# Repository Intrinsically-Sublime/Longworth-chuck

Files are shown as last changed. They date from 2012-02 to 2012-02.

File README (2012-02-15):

---Description---

Credit for the movement should go to the late Mr. Longworth of the Hunter Valley Woodturning Club, New South Wales, Australia.

Thanks to Hexitex for turning Mr. Longworth's desgin into a printable design.

All the files are oriented and scaled for printing already.

Changes

I Reduced its diameter to 85mm and changed it to a three jaw design. I then designed a system to lock it with out a wrench.

How the lock works

The front face is now supported by three short lengths of 5/16" (8mm) smooth rod that go through large holes in the guide and sit against the base. When you turn the lock ring it turns the planets/nuts that pull the guide back and it pulls the screws holding the jaws back against the now supported face.

( you could eliminate the smooth rods by making the outside of the face extend back far enough to rest on the lip of the base. )

Updates
jun 10/11 . Added jaw_guide.stl It keeps the jaws aligned while tightening.

jun 9/11 . Replaced jaws with angled jaws inspired by MarkU's design thingiverse.com/thing:9186 except mine are sloped on both sides so only one set is needed.

Video
youtube.com/watch?v=V_vG_LOLz4s
Instructions

--Four jaw version--

Simplified keyless chuck NOW WITH FOUR JAWS !!!!!!!!

This is untested but based on a working design.

I started over this time to guarantee symmetry.

Removed the need for smooth metal rod.

Increased thickness of face plate.

Added fourth jaw.

Increased ring gear strength.

Removed the need for machine screws with screw head or socket head. You can now use hex head bolts.

Only uses 8 machine screws / bolts with nuts.

Eight washers optional. (under planet gears and under the heads of the sliding jaw bolts)

Four springs optional. (between piston and base

---Instructions---

Printing
Turn off all extra shells when printing the gears and lock ring so you end up with solid teeth.

B.O.M.

six no.6 machine screws 2" long
six no.6 nuts.
one 5/16 nut (8mm nut)
three small thin washers
three pieces of 5/16 (8mm) smooth rod cut to 1.125" (28.5mm)
three springs (optional)

Test assemble all pieces and sand, shave, drill anything that causes friction.

Final assembly instructions

1) Install three screws in countersunk holes of guide. (slide springs over protruding screws)

2) Install three screws through slots in the guide the opposite direction as previous screws.

4) Install 5/16" (8mm) nut in the center of the base.

5) Install guide in to base being sure screws slide easily through holes in base.

6) Install nuts in planetary gears.

7) Install one planetary gear. You may want thin washers under the gears

8) Install lock ring and the second planetary gear.

9) Install third planetary gear by turning the last screw with a screwdriver.

10) Tighten all planetary gears evenly using screwdriver.

11) Glue screw heads to guide to ensure they don't turn any more.

12) Cut three pieces of 5/16 (8mm) smooth rod 1.125" (28.5mm) and slide them into holes in the guide.

13) Install face over the three screws protruding from slots in the guide.

14) Slide Jaw guide over protruding machine screws.

15) Install nuts in jaws and screw them to the screws protruding through face.

16) Loosen lock ring three turns.

17) Tighten jaw against the face until they are even.

18) Tighten lock ring until jaws are close to the face.

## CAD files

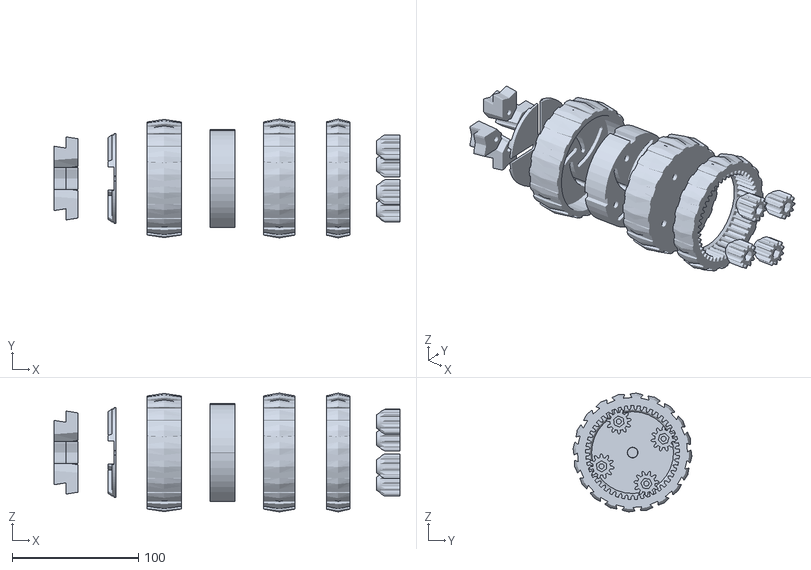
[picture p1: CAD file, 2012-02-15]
Four_jaw_chuck/Four_jaw_assembly.stl
274.5 x 94.3 x 94.3

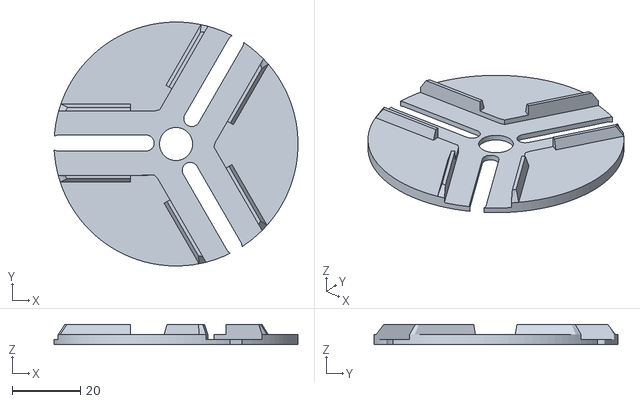
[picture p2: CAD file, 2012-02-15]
Three_jaw_chuck/Jaw_guide.stl
71.5 x 71.5 x 6.00

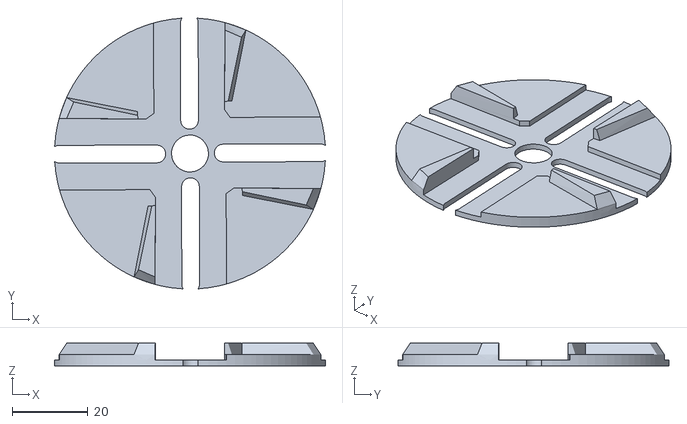
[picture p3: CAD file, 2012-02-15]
Four_jaw_chuck/Jaw_guide.stl
71.5 x 71.5 x 6.00

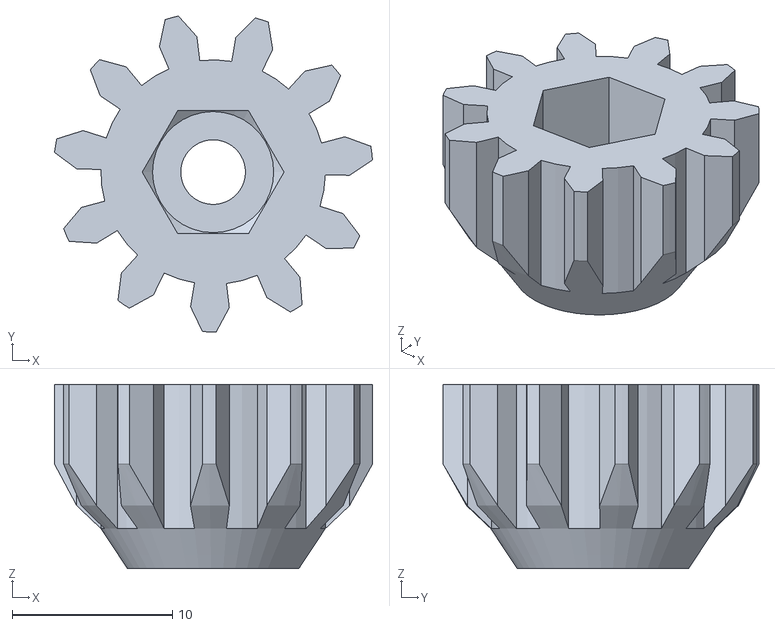
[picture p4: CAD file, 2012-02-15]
Three_jaw_chuck/Planet_gear.stl
19.8 x 19.7 x 11.5

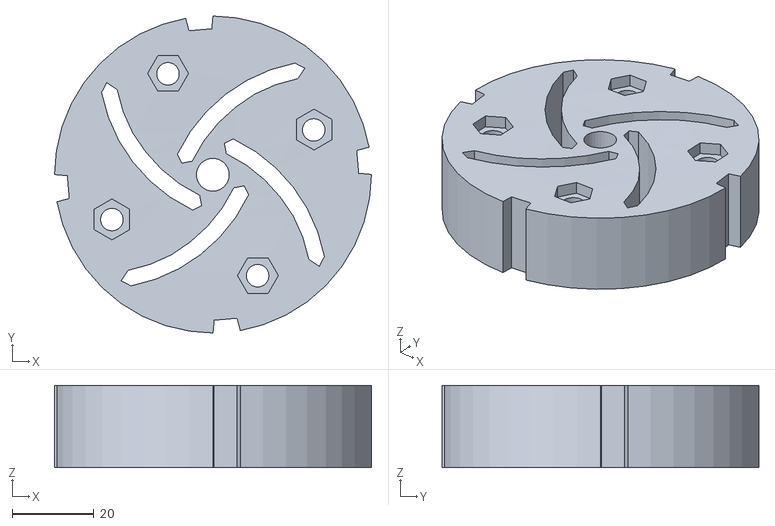
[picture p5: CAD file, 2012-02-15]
Four_jaw_chuck/Piston.stl
77.4 x 77.4 x 20.1

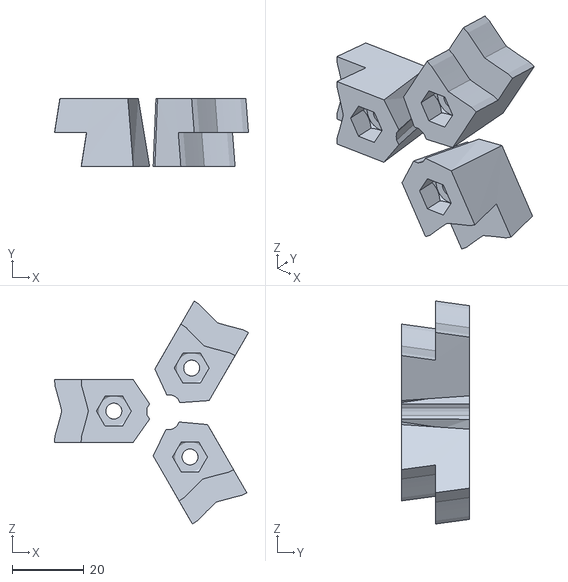
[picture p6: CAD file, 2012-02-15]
Three_jaw_chuck/transfer.stl
54.1 x 19.0 x 62.1

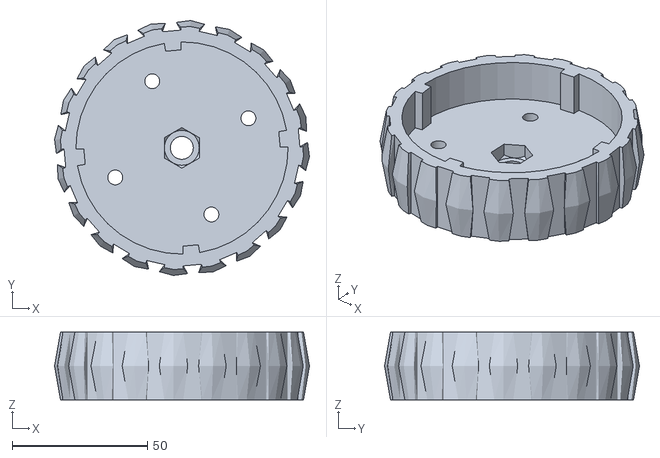
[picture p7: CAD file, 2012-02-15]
Four_jaw_chuck/Base.stl
94.3 x 94.3 x 25.0

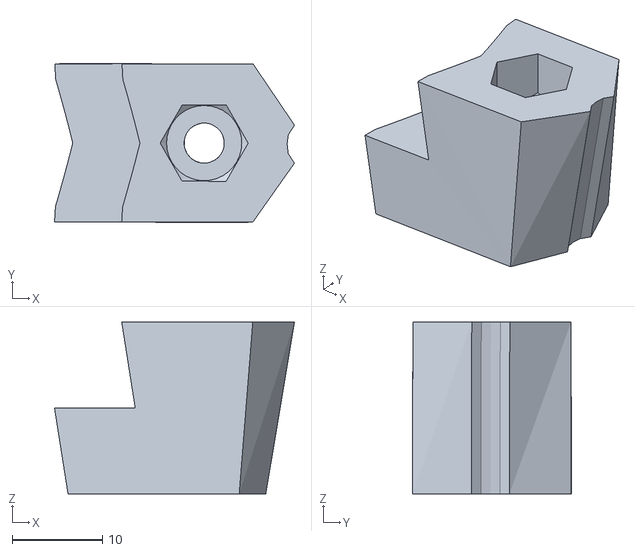
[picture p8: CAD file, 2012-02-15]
Three_jaw_chuck/Outside_jaw_v2.stl
26.5 x 17.5 x 19.0

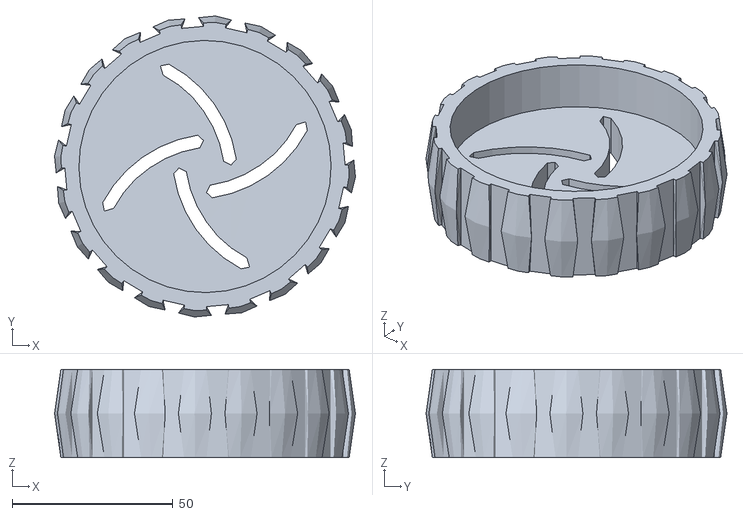
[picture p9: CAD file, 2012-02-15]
Four_jaw_chuck/Face.stl
93.7 x 93.7 x 27.5

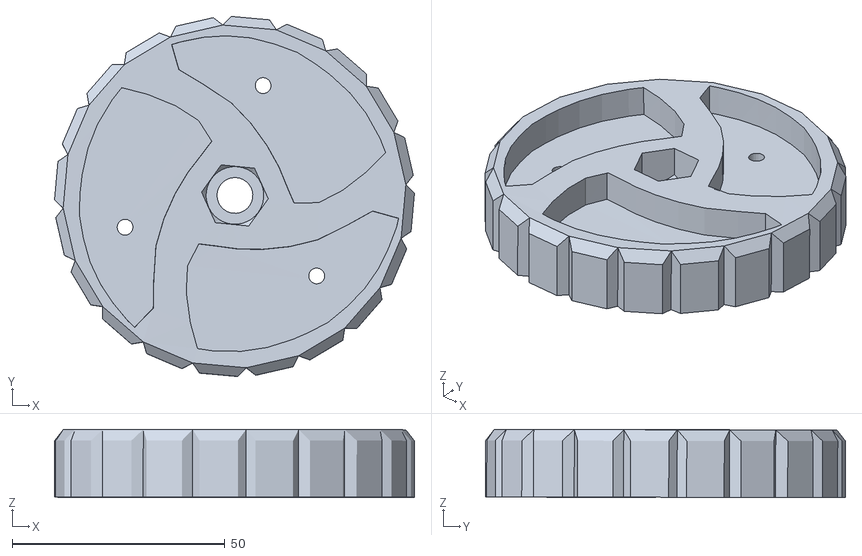
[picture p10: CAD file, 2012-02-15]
Three_jaw_chuck/Three_jaw_base.stl
84.6 x 84.6 x 16.0

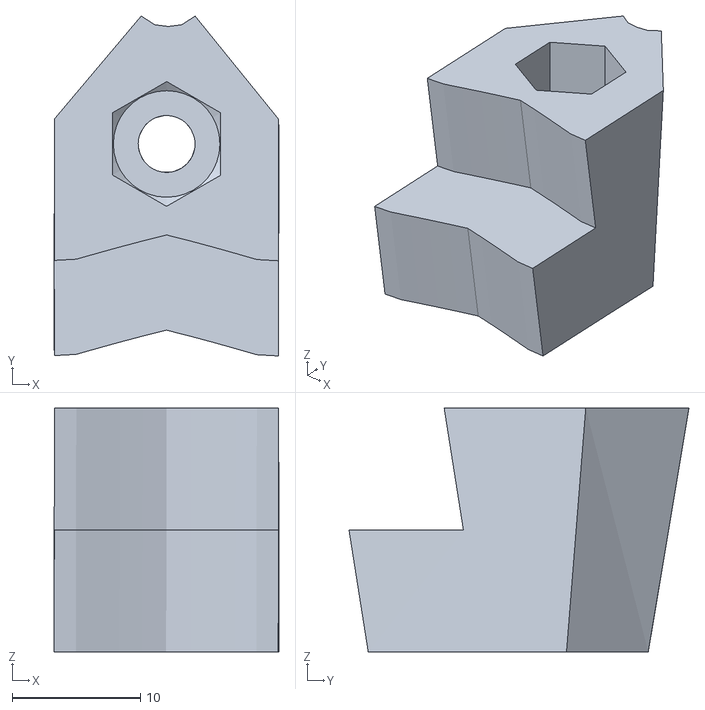
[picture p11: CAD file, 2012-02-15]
Four_jaw_chuck/Jaws.stl
17.5 x 26.5 x 19.0

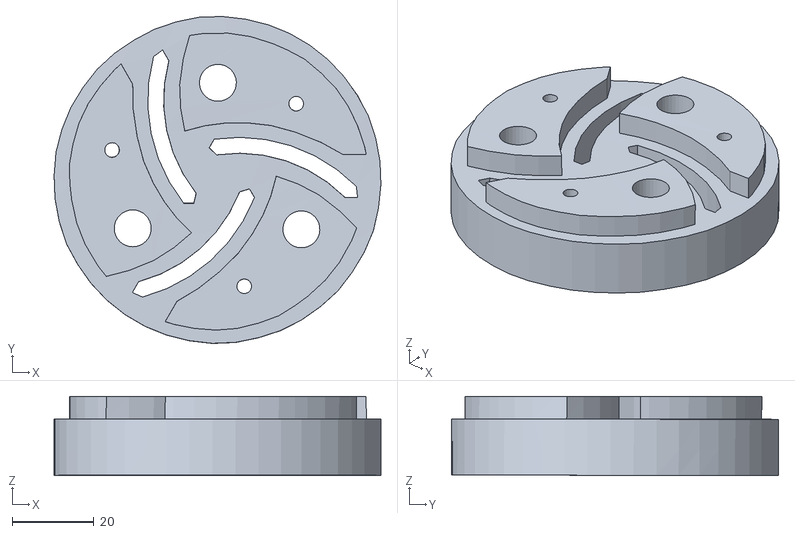
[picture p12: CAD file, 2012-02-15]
Three_jaw_chuck/Three_jaw_guide.stl
79.7 x 79.8 x 19.3

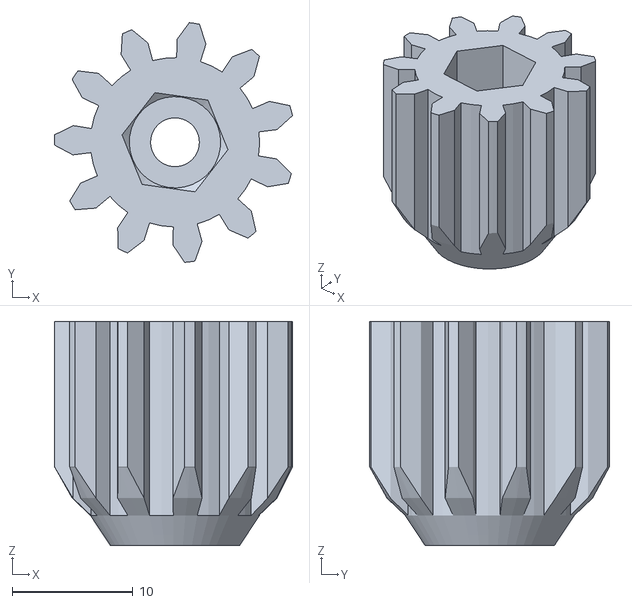
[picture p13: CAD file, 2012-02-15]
Four_jaw_chuck/Planet_gears.stl
19.7 x 19.8 x 18.6

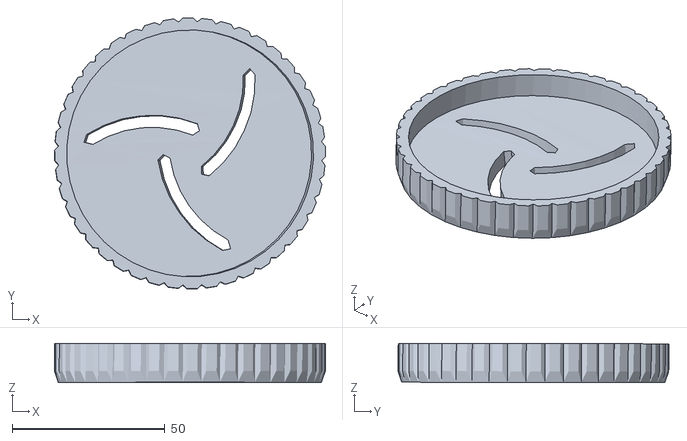
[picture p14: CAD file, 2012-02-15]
Three_jaw_chuck/Three_jaw_face.stl
88.6 x 88.6 x 12.9

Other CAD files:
Four_jaw_chuck/Lock_ring.stl
Three_jaw_chuck/Three_jaw_chuck.stl
Three_jaw_chuck/Lock_ring.stl
Four_jaw_chuck/Four_jaw.blend
Three_jaw_chuck/Three_jaw_chuck.blend
